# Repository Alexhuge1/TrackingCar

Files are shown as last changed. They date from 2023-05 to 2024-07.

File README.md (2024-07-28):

# TrackingCar
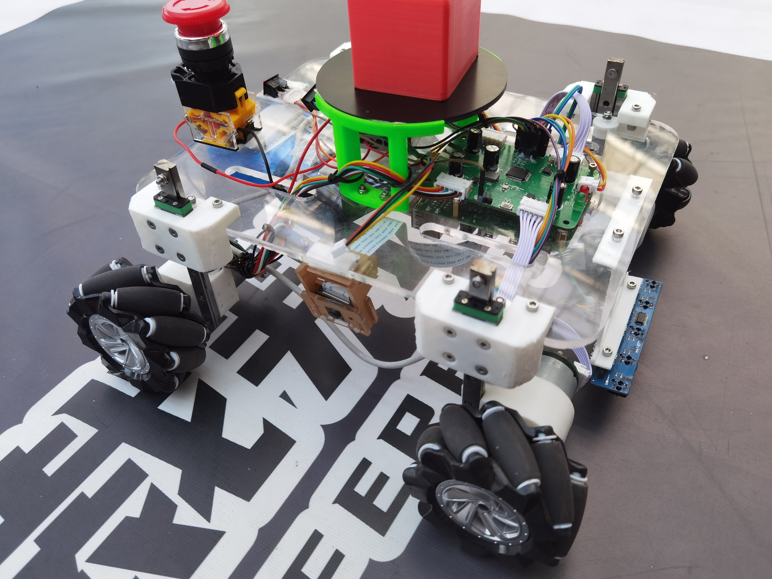
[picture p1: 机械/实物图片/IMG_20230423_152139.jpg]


比赛规则，沿着赛道循迹一圈冲过终点，其中道路有障碍物要做一定量的减震，并且要与树莓派通信实现识别红绿灯并在主板上点亮相对应的灯。

硬件方面：小车电流较小并且为了走线方便，采用将主控与电机驱动放一块板子上的方式，小车使用了STM32F103RCT6作为主控，A4950做电机驱动芯片，树莓派4B做视觉识别，MP2482转压芯片做12V转5V，AMS1117-3.3转压芯片做5V转3.3V，并加了一个急停开关便于调试

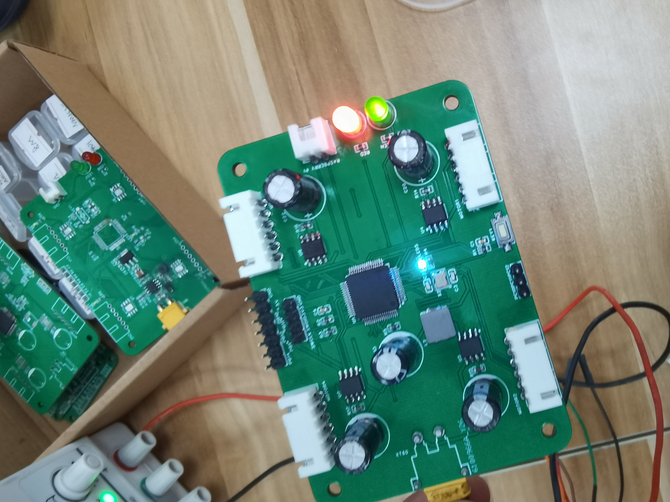
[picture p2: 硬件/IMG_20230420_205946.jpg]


机械方面：亚克力作为中间支撑，四周采用滑块做悬挂，并且训练使用麦克纳姆轮（其实没有必要，这次只用了差速转向）



电控方面：对于循迹传感器做逻辑判断，并且使用双路PWM输出控制电机

视觉方面：采用了树莓派做边缘计算载体，调用opencv库识别红绿灯并且对环境光进行过滤

小车制作：机械主要靠3D打印和亚克力切割，电路板自行焊接，所有配件都基本为标准件，淘宝可以买到滑轨和联轴器麦轮这类。

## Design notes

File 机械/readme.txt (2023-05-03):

.LOG

Summary and reflection：

	3D打印留够余量
	减重设计与结构简化，如无必要，勿增实体
	把握材料的力学强度
	弹簧劲度系数公式
	拉簧与压簧的区别
	亚克力板切割相关：精度问题，队里精度很拉，创新创业学院精度尚可；切割深度问题，如未切穿，切勿移动，调整切割深度再次切割即可
	全局意识，优先考虑整体布局，eg：某个因检录不合格重打了5次连接件

	——xhw

	整个车体设计是为了减震，其实从设计来说是不合格的，
	从车的前面来看，y轴的受力是依靠亚克力板的，z轴的整个车体的承重只有依靠弹簧和滑轨，这样的张力和材料使用是不合理的
	还有就是设计和优化问题，先生成装配体然后一定要先出demo，然后再改进，不然会影响电控和硬件测试。
	—hy

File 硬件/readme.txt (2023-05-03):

.LOG

tip：
	我使用嘉立创eda支持国产而且好用，队里用AD可以都学一下，嘉立创可以直接在立创商城找到元件
	这次PCB用PCB6，总共被学姐要求回去改了六版，每次还有一点小问题就不好修，只好重新布局，其实以后看感觉还是挺傻的，不过现在刚学，情有可原，一些感悟分享一下，有帮助就满足了。

Summry and reflection:

	使用嘉立创eda专业版打开
	从投板到收到pcb总共时间大概在5天-7天
	画板子原理图一定要仔细，要去看参考手册，读它的sheet和参考电路原理图和建议布板方式。
	先画芯片的外围电路，就是reset晶振这些，先确保没问题，和同学对一下或者问优秀的学长学姐

	一些技术感悟：
	首先是原理图，先画芯片引脚，然后画外围最小系统，然后画一些转压，然后驱动板（其实强电弱电一定要分开，不过这次只有四个电机驱动，总电流不会超过1A，我就集成一下）
	记得排版好看一点，这在焊接或者交流的时候大有帮助。
	1.芯片如果外接rtc，布线不要打孔。
	2.12V5V这些稍微高压的增加线径，看对照表，估算电流
	3.画电路板的时候最好一次性画好（如果比较小，比如这次）
	4.一定要考虑好布局，布局的时候一个模块一个模块布局，不然你的布线会十分困难
	5.如果经济允许，可以自己去淘宝优信电子这类的网站配一套bom，然后自己买两本容阻本，不求人，这次芯片问题浪费我好多时间
	6.焊接时候，先焊接芯片，然后焊接转压，先测试转压是否好使，然后再通电给到芯片，不然就是点亮一颗芯片了
	这个文档可以不断更新，如果你们有什么感悟也可以不断添加
	——2023/4/25 hy

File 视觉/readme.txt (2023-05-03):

.LOG

tip：
	文件需要在Linux环境下执行

Summry and reflection:

	makefile与cmakelists的编写
	树莓派远程调试：nomachine、vnc
	环境光过滤

	——xhw

11:01 2023/4/25

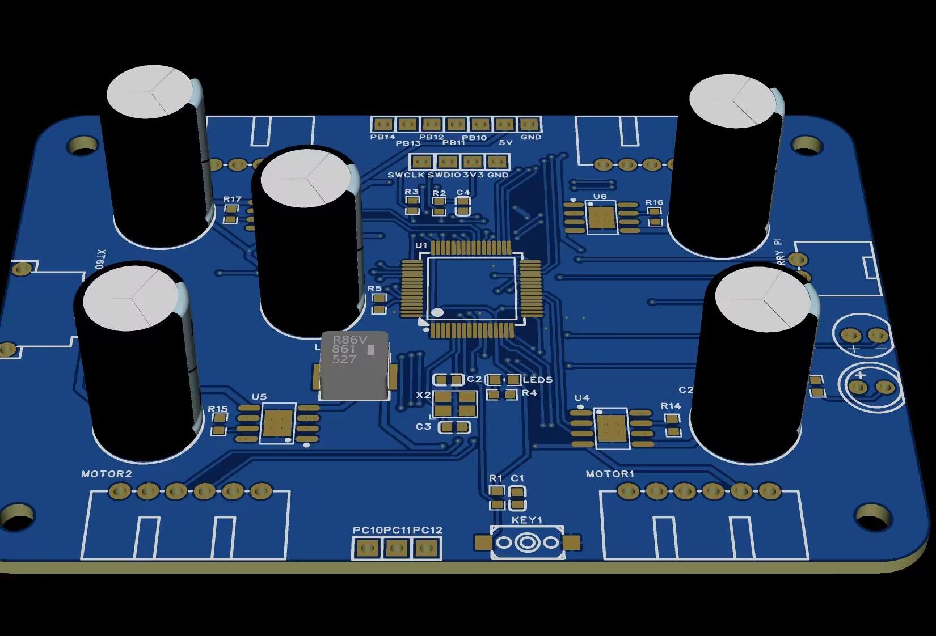
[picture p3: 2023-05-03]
硬件/第六版.jpg

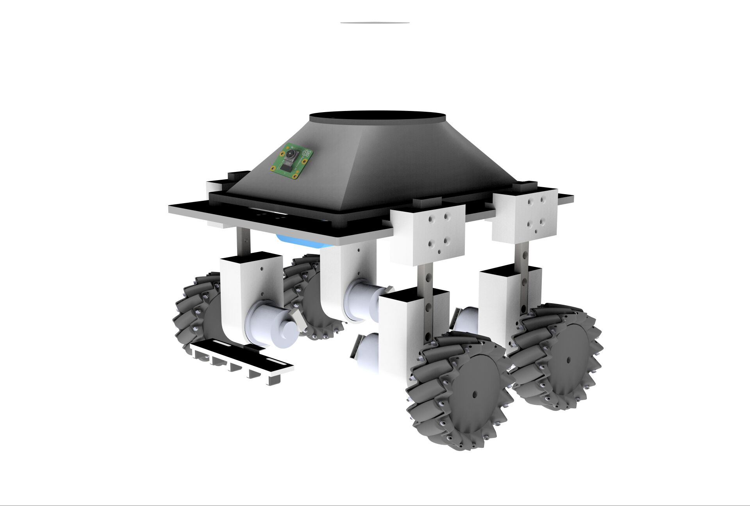
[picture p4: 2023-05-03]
机械/实物图片/18fcba3be2038c55.jpg

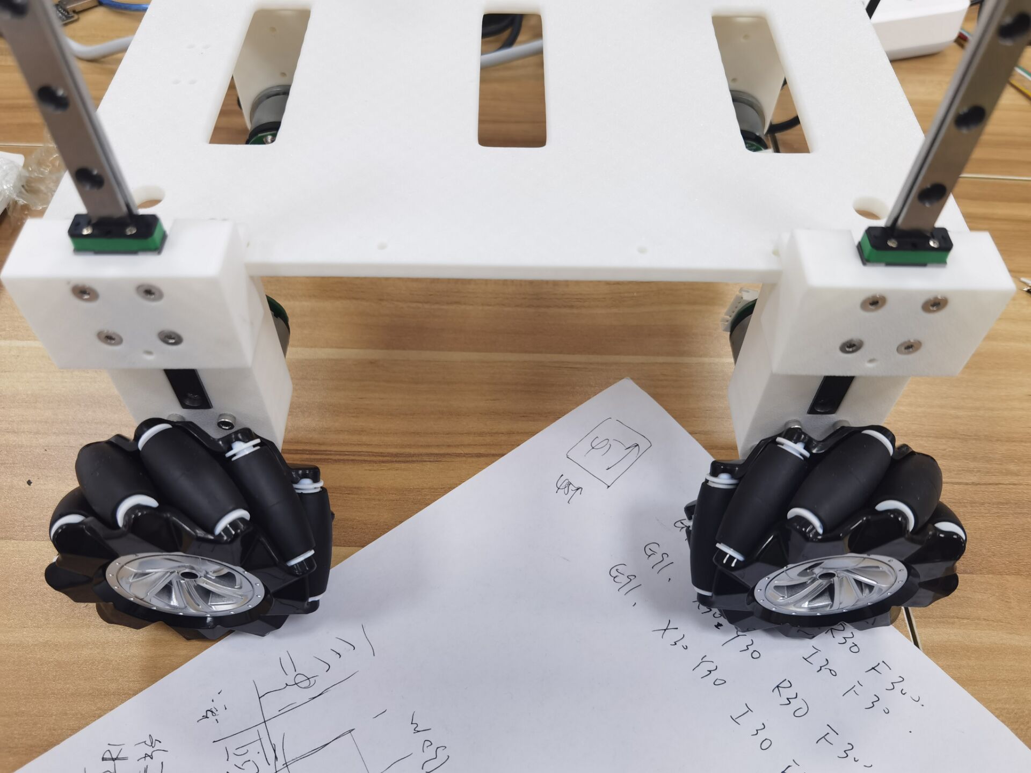
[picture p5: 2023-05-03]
机械/实物图片/初版本.jpg

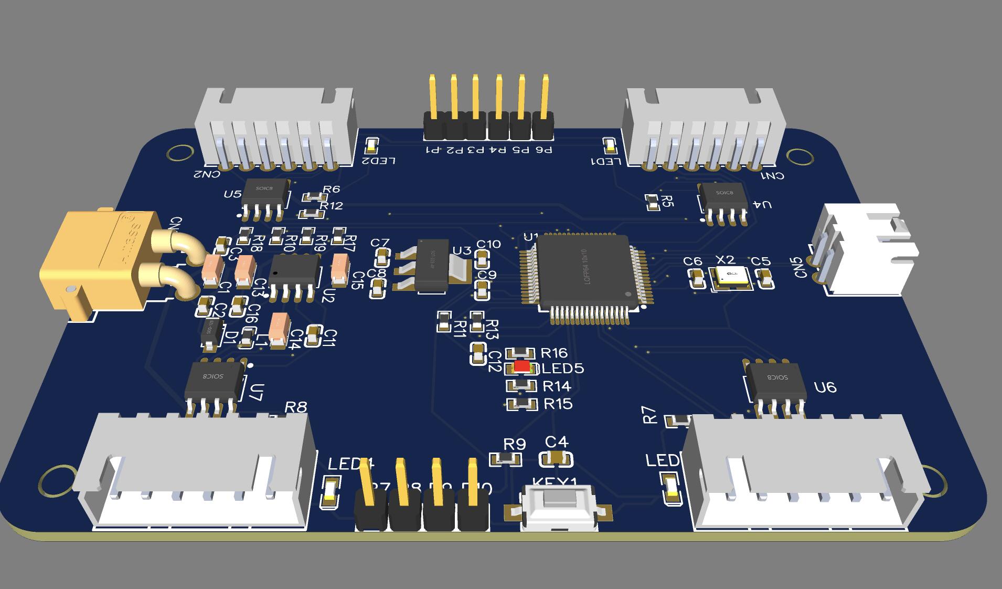
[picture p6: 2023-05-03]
硬件/第三版.jpg

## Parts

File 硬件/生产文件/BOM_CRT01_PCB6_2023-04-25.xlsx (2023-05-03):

No. | Quantity | Comment | Designator | Footprint | Value | Manufacturer Part | Supplier Part | Supplier | 3D Model | 3D Model Title | Crystal Type | Manufacturer
1 | 14 | Header-Male-2.54_1x1 | 3V3,5V,GND,GND,PB10,PB11,PB12,PB13,PB14,PC10,PC11,PC12,SWCLK,SWDIO | HDR-TH_1P-P2.54-V-M |  | 2.54-1*1P针 | C81276 | LCSC |  |  |  | BOOMELE(博穆精密)
2 | 1 | AMS1117-3.3V | AMS1117 | SOT-223-4_L6.5-W3.5-P2.30-LS7.0-BR |  | AMS1117-3.3V | C2688239 | LCSC |  |  |  | WPMtek(维攀微)
3 | 1 | 0.1uF | C1 | C0603
4 | 2 | 22pf | C2,C3 | C0603
5 | 1 | 0.1u | C4 | C0603
6 | 2 | 10uF | C5,C7 | C0603
7 | 2 | 100nF | C6,C8 | C0603
8 | 1 | 22uf | C10 | C1206 | 22uf | C3216X5R1V226MTJ00E | C342620 | LCSC | e4be705b945545a48e666415e3682bd8 | C1206_L3.2-W1.6-H1.3 |  | TDK
9 | 1 | 1uF | C11 | C0603
10 | 1 | 0.1uF | C12 | CASE-A_3216
11 | 5 | 100uF | C13,C18,C20,C22,C23 | CAP-TH_BD10.0-P5.00-D1.0-FD | 100uF | RGA101M2ABK-1020 | C134550 | LCSC | 6ce78ce5315348e095d700085da75e48 | CAP-TH_D10.0-H16.0-P5.00 |  | lelon(立隆)
12 | 4 | 0.22uf | C14,C15,C16,C17 | C0603 | 0.22uf |  |  |  | ac125912035d415993ca9572d50418b1 | C0603_L1.6-W0.8-H0.8
13 | 1 | STPS0560Z | D1 | SOD-123_L2.7-W1.6-LS3.7-RD |  | STPS0560Z | C99285 | LCSC |  |  |  | ST(意法半导体)
14 | 1 | K2-3.6×6.1_SMD | KEY1 | KEY-SMD_2P-L6.2-W3.6-LS8.0 |  | K2-1107ST-A4SW-06 | C118141 | LCSC
15 | 1 | 4.7uH | L2 | IND-SMD_L6.4-W6.0 | 4.7uH | ETQP3M4R7KVN | C412308 | LCSC | ee8a43eb84ef436b9dc6a9425abef009 | IND-SMD_L6.4-W6.0-H3.0 |  | PANASONIC(松下)
16 | 1 | LED-0603_R | LED5 | LED0603_RED |  | 19-217/R6C-AL1M2VY/3T | C72044 | LCSC |  |  |  | EVERLIGHT(台湾亿光)
17 | 1 | 333-2SYGD/S530-E2-L | LED7 | LED-TH_BD5.0-P2.54-FD |  | 333-2SYGD/S530-E2-L | C99697 | LCSC |  |  |  | EVERLIGHT(亿光)
18 | 1 | XL-502SURD | LED8 | LED-TH_BD5.9-P2.54-RD_RED |  | XL-502SURD | C2895492 | LCSC |  |  |  | XINGLIGHT(成兴光)
19 | 4 | HX25003-6WAP | MOTOR1,MOTOR2,MOTOR3,MOTOR4 | CONN-TH_6P-P2.50_HX25003-6WAP |  | HX25003-6WAP | C442330 | LCSC |  |  |  | HX(红星)
20 | 5 | 10K | R1,R2,R3,R5,R6 | R0603
21 | 2 | 1k | R4,R9 | R0603
22 | 2 | 100 | R7,R8 | R0603
23 | 1 | 100k | R11 | R0603
24 | 1 | 7.6k | R12 | R0603
25 | 1 | 40.2k | R13 | R0603
26 | 4 | 0.25 | R14,R15,R16,R17 | R0603
27 | 1 | 18.7k | R18 | R0603 | 18.7k |  |  |  | 3281a289d46d4bb1877be1eabd090e13 | R0603_L1.6-W0.8-H0.8
28 | 1 | HX25035-2WAP | RASPBERRY PI | CONN-TH_2P-P2.50_HX25035-2WAP |  | HX25035-2WAP | C442383 | LCSC |  |  |  | HX(Zhejiang Yueqing Hongxing Elec)
29 | 1 | STM32F103RCT6 | U1 | LQFP-64_L10.0-W10.0-P0.50-LS12.0-BL |  | STM32F103RCT6 | C8323 | LCSC |  |  |  | ST(意法半导体)
30 | 1 | MP2482DN-LF-P | U2 | ESOP-8_L4.9-W3.9-P1.27-LS6.0-BL-EP-1 |  | MP2482DN-LF-P | C9900000581 | LCSC |  |  |  | null
31 | 4 | A4950ELJTR-T | U4,U5,U6,U7 | SOIC-8_L4.9-W3.9-P1.27-LS6.0-BL-EP |  | A4950ELJTR-T | C82404 | LCSC |  |  |  | ALLEGRO(美国埃戈罗)
32 | 1 | - | X2 | OSC-SMD_4P-L3.2-W2.5-BL |  | 1C208000BC0K | C253746 | LCSC |  |  |  | KDS(大真空)
33 | 1 | XT30PW-M | XT30 | CONN-TH_XT30PW-M |  | XT30PW-M | C431092 | LCSC |  |  |  | AMASS(艾迈斯)

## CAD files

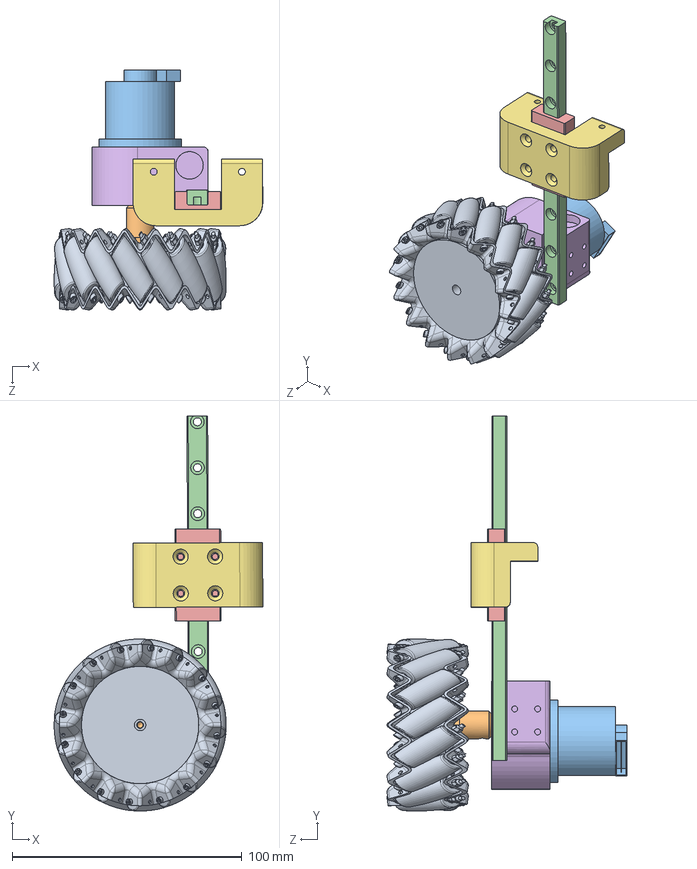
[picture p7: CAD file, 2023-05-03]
机械/车体模型/轮系.SLDASM
90.8 x 171.9 x 104.5 mm
麦轮左旋
标准件-联轴器
电控原件-电机
标准-导轨 MGN9
标准-滑块 MGN9H
轮系_打印件
机架打印件

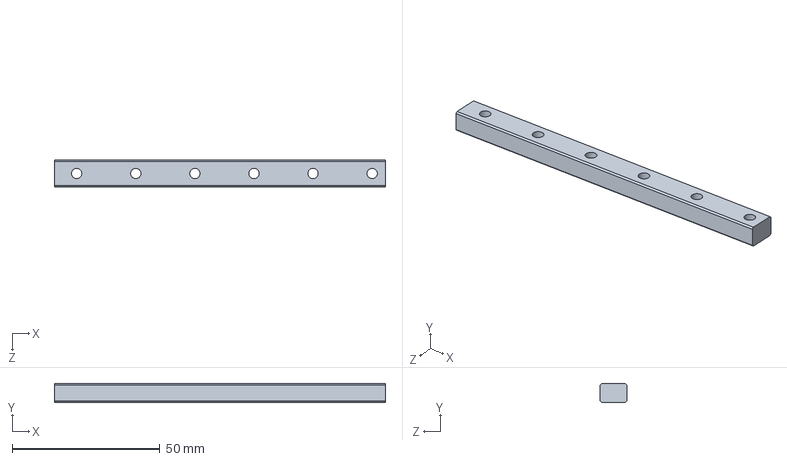
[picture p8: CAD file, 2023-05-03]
机械/车体模型/标准-导轨 MGN9.SLDPRT
112.0 x 6.50 x 9.00 mm

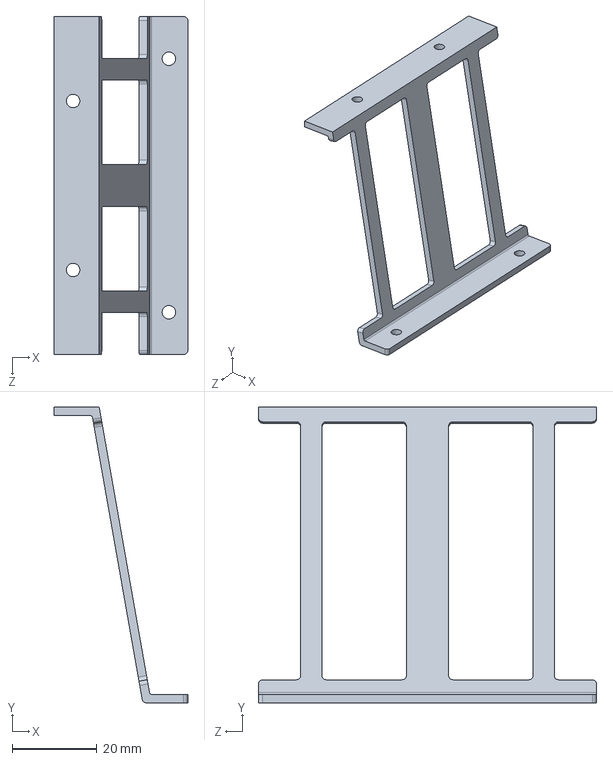
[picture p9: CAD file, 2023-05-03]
机械/车体模型/寻迹传感器固定件.SLDPRT
31.7 x 70.0 x 80.0 mm

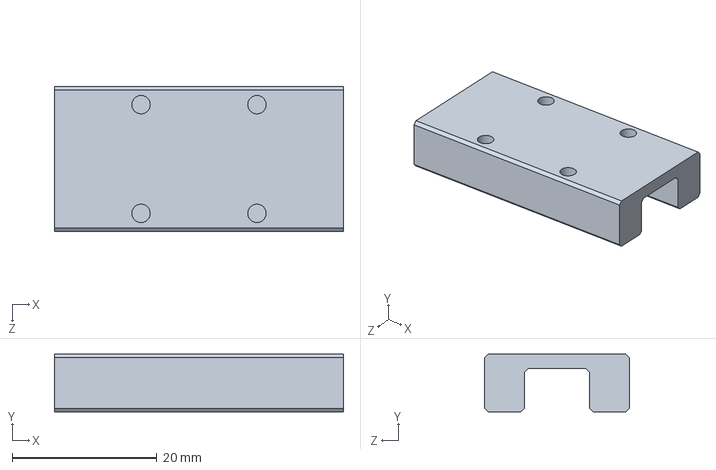
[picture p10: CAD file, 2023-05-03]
机械/车体模型/标准-滑块 MGN9H.SLDPRT
39.9 x 8.00 x 20.0 mm

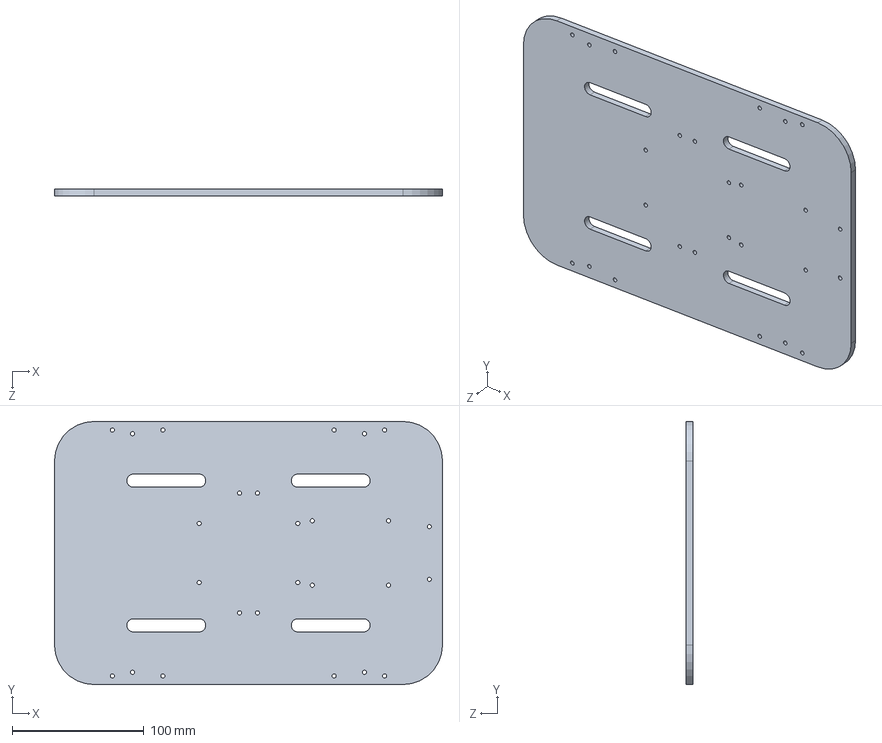
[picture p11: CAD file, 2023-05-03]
机械/车体模型/亚克力板.SLDPRT
295.0 x 200.0 x 5.00 mm

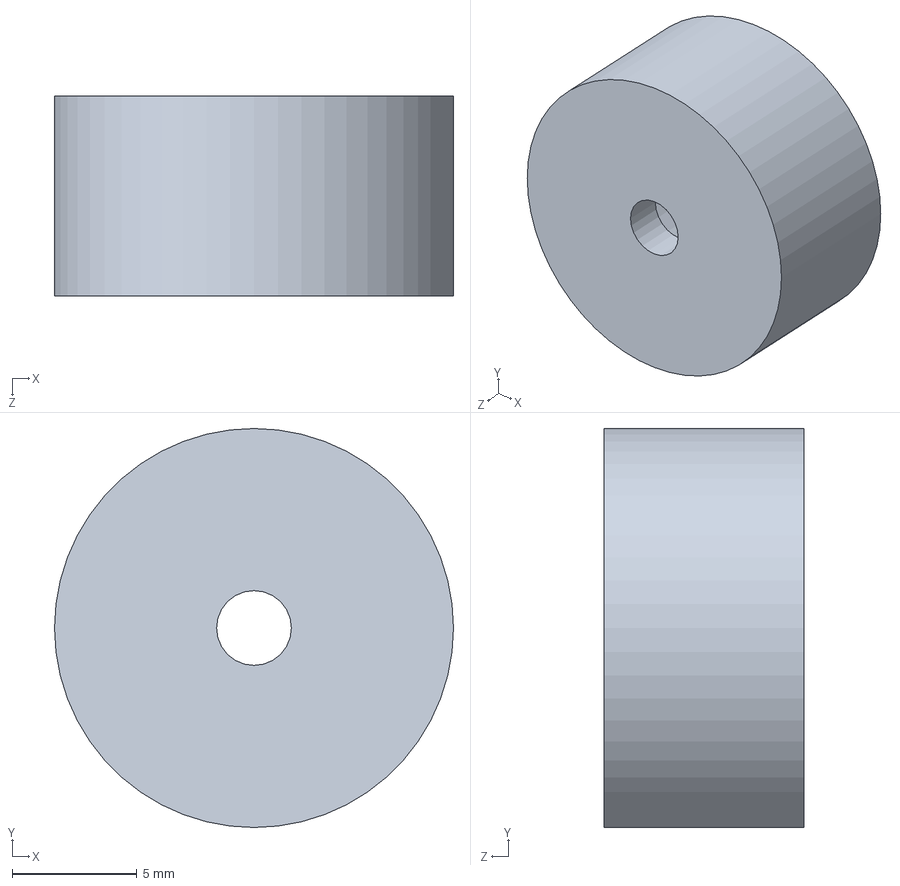
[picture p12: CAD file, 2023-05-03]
机械/车体模型/弹簧固定_打印件.SLDPRT
16.0 x 16.0 x 8.00 mm

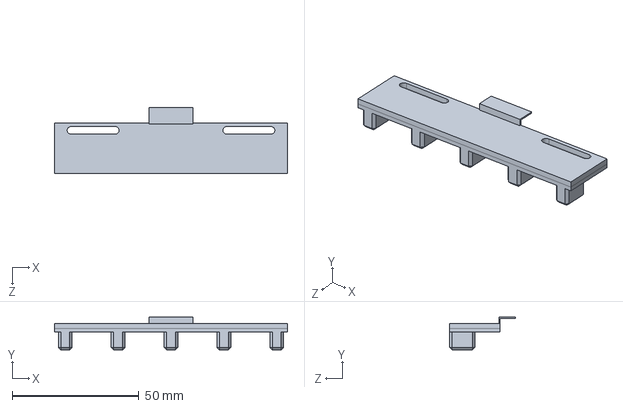
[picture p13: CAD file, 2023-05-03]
机械/车体模型/电控元件-寻迹模块.SLDPRT
92.0 x 13.0 x 26.0 mm

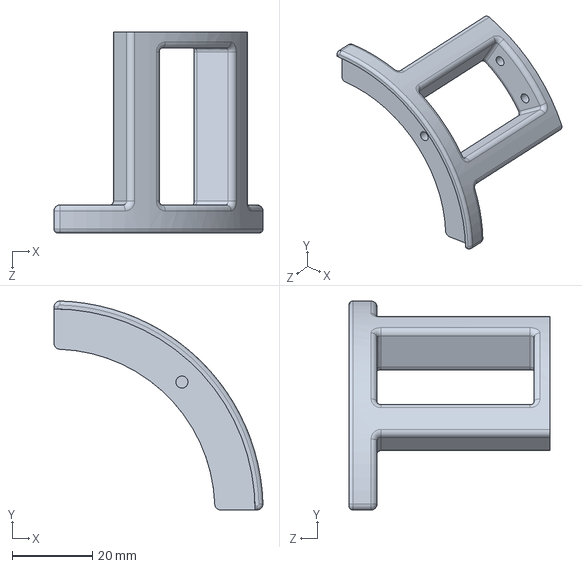
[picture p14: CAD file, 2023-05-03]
机械/车体模型/载物平台固定_打印件.SLDPRT
52.0 x 52.0 x 50.0 mm

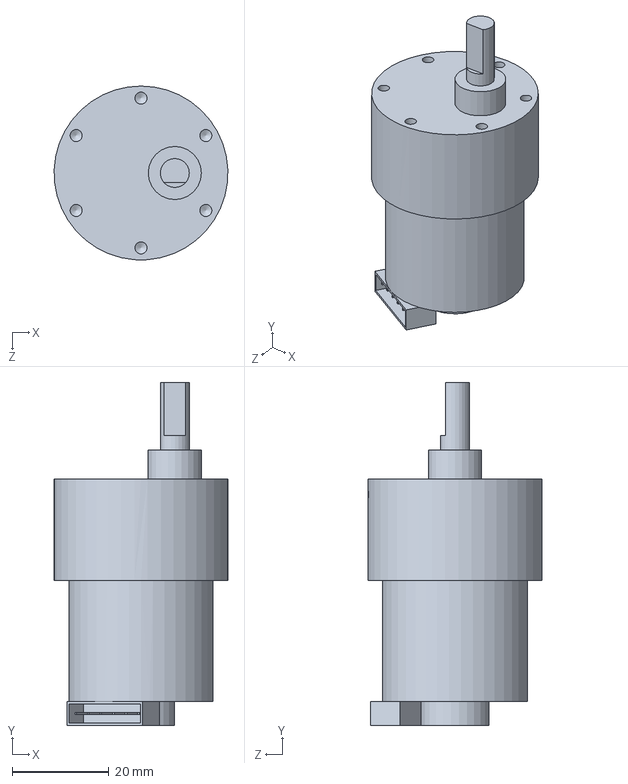
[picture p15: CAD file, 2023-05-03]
机械/车体模型/电控原件-电机.SLDPRT
36.0 x 71.0 x 36.0 mm

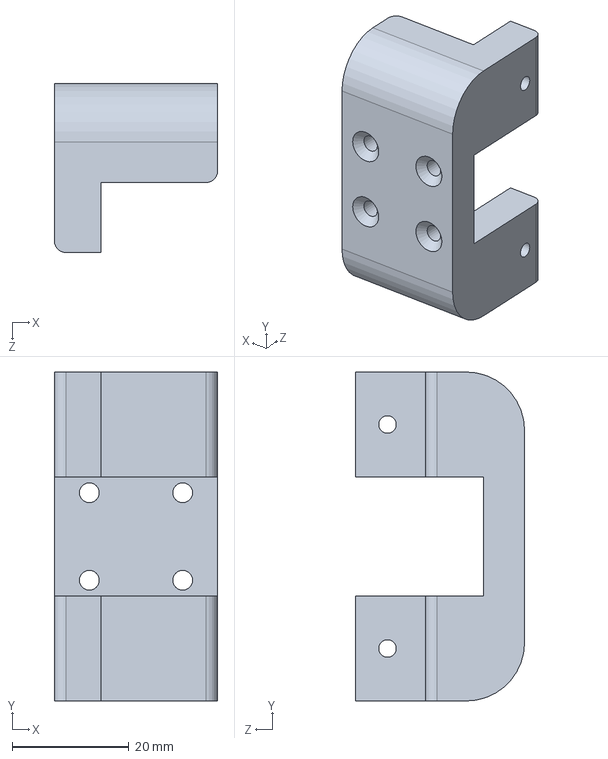
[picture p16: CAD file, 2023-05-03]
机械/车体模型/机架打印件.SLDPRT
28.0 x 56.4 x 29.0 mm

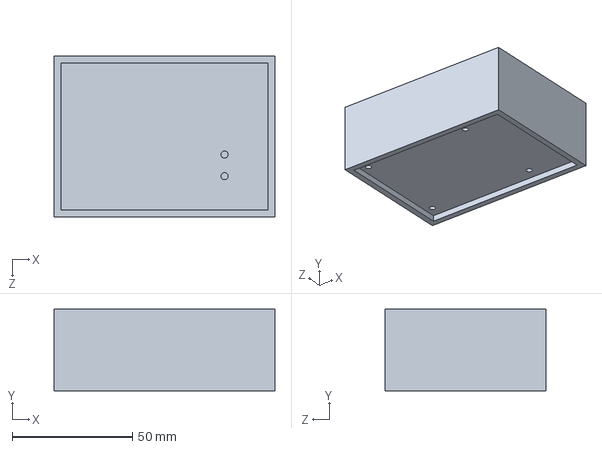
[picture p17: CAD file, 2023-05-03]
机械/车体模型/树莓派外壳.SLDPRT
92.0 x 34.0 x 67.0 mm

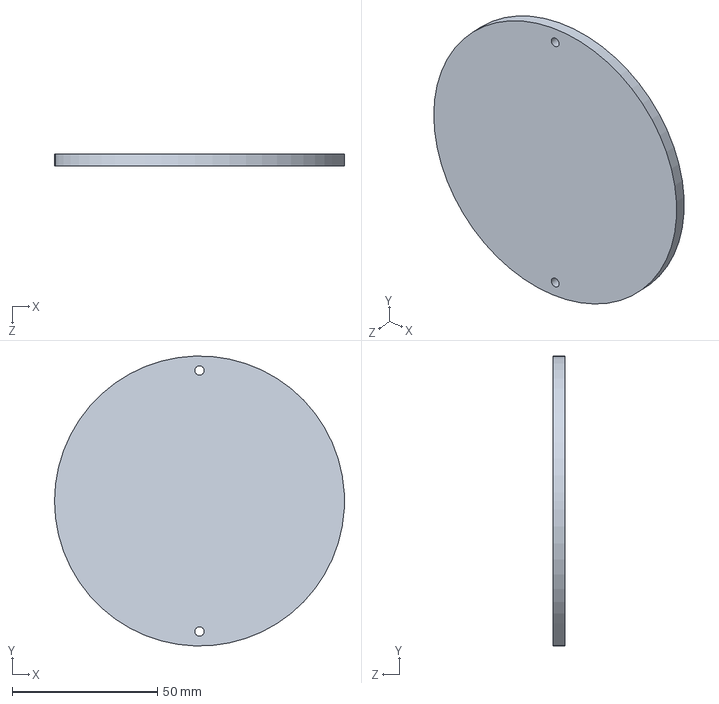
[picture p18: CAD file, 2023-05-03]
机械/车体模型/承载板.SLDPRT
100.0 x 100.0 x 4.00 mm

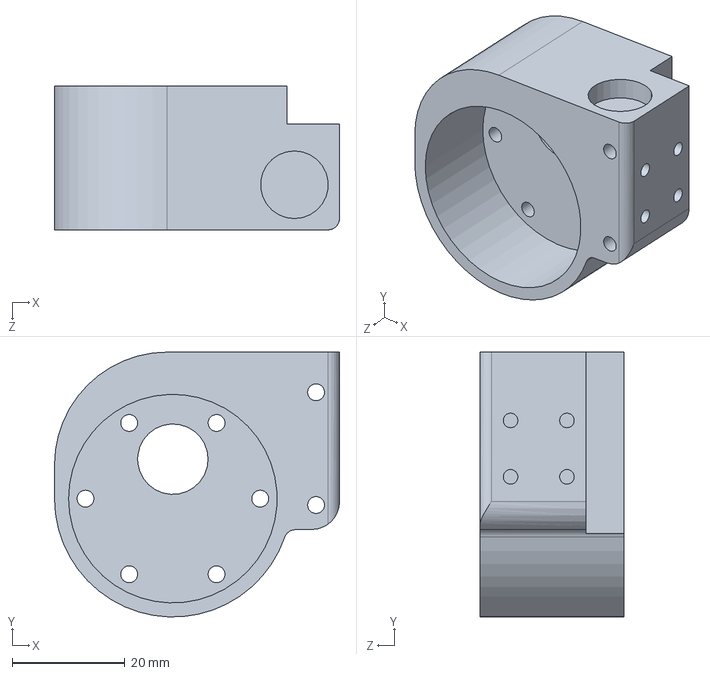
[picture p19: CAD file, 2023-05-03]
机械/车体模型/轮系_打印件_镜像.SLDPRT
50.6 x 47.0 x 25.5 mm

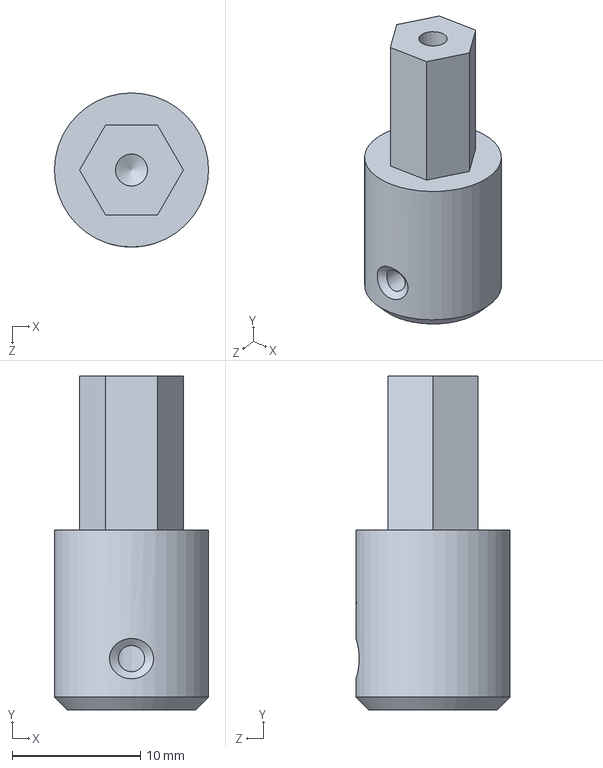
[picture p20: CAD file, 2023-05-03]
机械/车体模型/标准件-联轴器.SLDPRT
12.0 x 26.0 x 12.0 mm

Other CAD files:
机械/车体模型/轮系 _镜像.SLDASM
机械/车体模型/弹簧.SLDPRT
机械/车体模型/轮系_打印件.SLDPRT
